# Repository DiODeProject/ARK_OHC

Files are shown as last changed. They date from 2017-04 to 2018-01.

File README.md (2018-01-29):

# ARK - Overhead Controller of Sheffield Robotics

Here we provide the Eagle files (schematics, layouts and gerbers) for the implementation of the new Overhead Controller (OHC) for the Kilobots. 

The bootloader for the microcontroller (Atmega328, 16MHZ) is the same as the Arduino Pro Mini and can be found here: https://github.com/arduino/Arduino/tree/master/hardware/arduino/avr/bootloaders/atmega 

The software for the microcontroller can be found here: https://github.com/acornejo/kilolib. 
Because we use 6 IR LED boards instead of 1, in file `ohc.c` we need to change line 33 to `#define ir_mask 0b00111111 | PORTB`. And then compile on the terminal as `make arduino-ohc-16mhz`.

## Citation
If you make use of or extend this design please cite:

* Nikolaidis, E., Sabo, C., Marshall, J. A. R., Reina, A. (2017) Characterisation and upgrade of the communication between overhead controllers and Kilobots. doi: [10.15131/shef.data.4990910.v2](https://figshare.com/articles/Characterisation_and_upgrade_of_the_communication_between_overhead_controllers_and_Kilobots/4990910)

## See Also
* [KilobotArena](https://github.com/DiODeProject/KilobotArena)
* [Kilobot Wiki](http://diode.group.shef.ac.uk/kilobots/index.php/Kilobots)

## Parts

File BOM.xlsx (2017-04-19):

Board | Name | Quantity | Details | Average cost | Total Cost
Controller | 2.1mm Right Angle PCB Mount DC Power Socket 2.5A | 1 | For the power supply | 0.75 £ | Total cost of the components 12.32 £ Cost of the PCB 50 £ (for 1 board)
 | 2.1mm dc plug | 1 |  | 0.75 £
 | atgmega328-au | 1 | Microcontroller | 4.6 £
 | ft232rl | 1 | Usb to serial interface | 1 £
 | Mount Female Type B USB Connector | 1 |  | 0.45 £
 | BSR802N L6327 N-channel MOSFET | 6 | MOSFET Switches | 1.2 £
 | 22pf Capacitor | 2 | Case 0603 | 0.7 £
 | 0.1uf Capacitor | 7 | Case 0603 | 0.2 £
 | 10uf/50V Capacitor | 1 |  | 0.2 £
 | 470uf/25V Capacitor | 1 |  | 0.6 £
 | 1KΩ Resistor | 2 | Case 0603 | 0.2 £
 | 10KΩ Resistor | 1 |  | 0.1 £
 | 100Ω Resistor | 6 |  | 0.3
 | 47ΚΩ Resistor | 6 |  | 0.07 £
 | 16Mhz Crystal | 1 |  | 0.2 £
 | LED red | 1 | Case 0603 | 0.1 £
 | LED green | 1 |  | 0.1 £
 | SMD tactile push button | 1 |  | 0.3 £
 | female headers 6x1 + 2x1 | 1 |  | 0.3 £
 | male header 3x2 | 1 |  | 0.2 £
IR LED | IR LED TSAL6200 | 10 | Infrared LEDs | 1 £ | Total cost of the components 1.2 £ Cost of the LED PCB 50 £ (for 1 board)
 | 1Ω Resistor | 5 | Case 1206 | 0.2 £

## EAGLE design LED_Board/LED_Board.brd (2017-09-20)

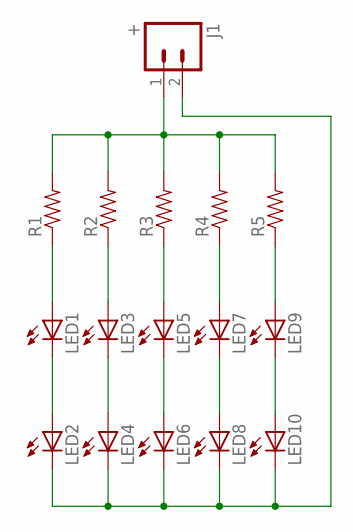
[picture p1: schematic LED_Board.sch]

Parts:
J1: +; 1X02_LOCK
LED1, LED2, LED3, LED4, LED5, LED6, LED7, LED8, LED9, LED10: LED5MM
R1, R2, R3, R4, R5: RESISTOR1206; 1206

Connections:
GND: J1.2, LED2.K (C), LED4.K (C), LED6.K (C), LED8.K (C), LED10.K (C)
unnamed: J1.1, R1.2, R2.2, R3.2, R4.2, R5.2
unnamed: LED9.A, R5.1
unnamed: LED7.A, R4.1
unnamed: LED5.A, R3.1
unnamed: LED3.A, R2.1
unnamed: LED1.A, R1.1
unnamed: LED1.K (C), LED2.A
unnamed: LED3.K (C), LED4.A
unnamed: LED5.K (C), LED6.A
unnamed: LED7.K (C), LED8.A
unnamed: LED9.K (C), LED10.A

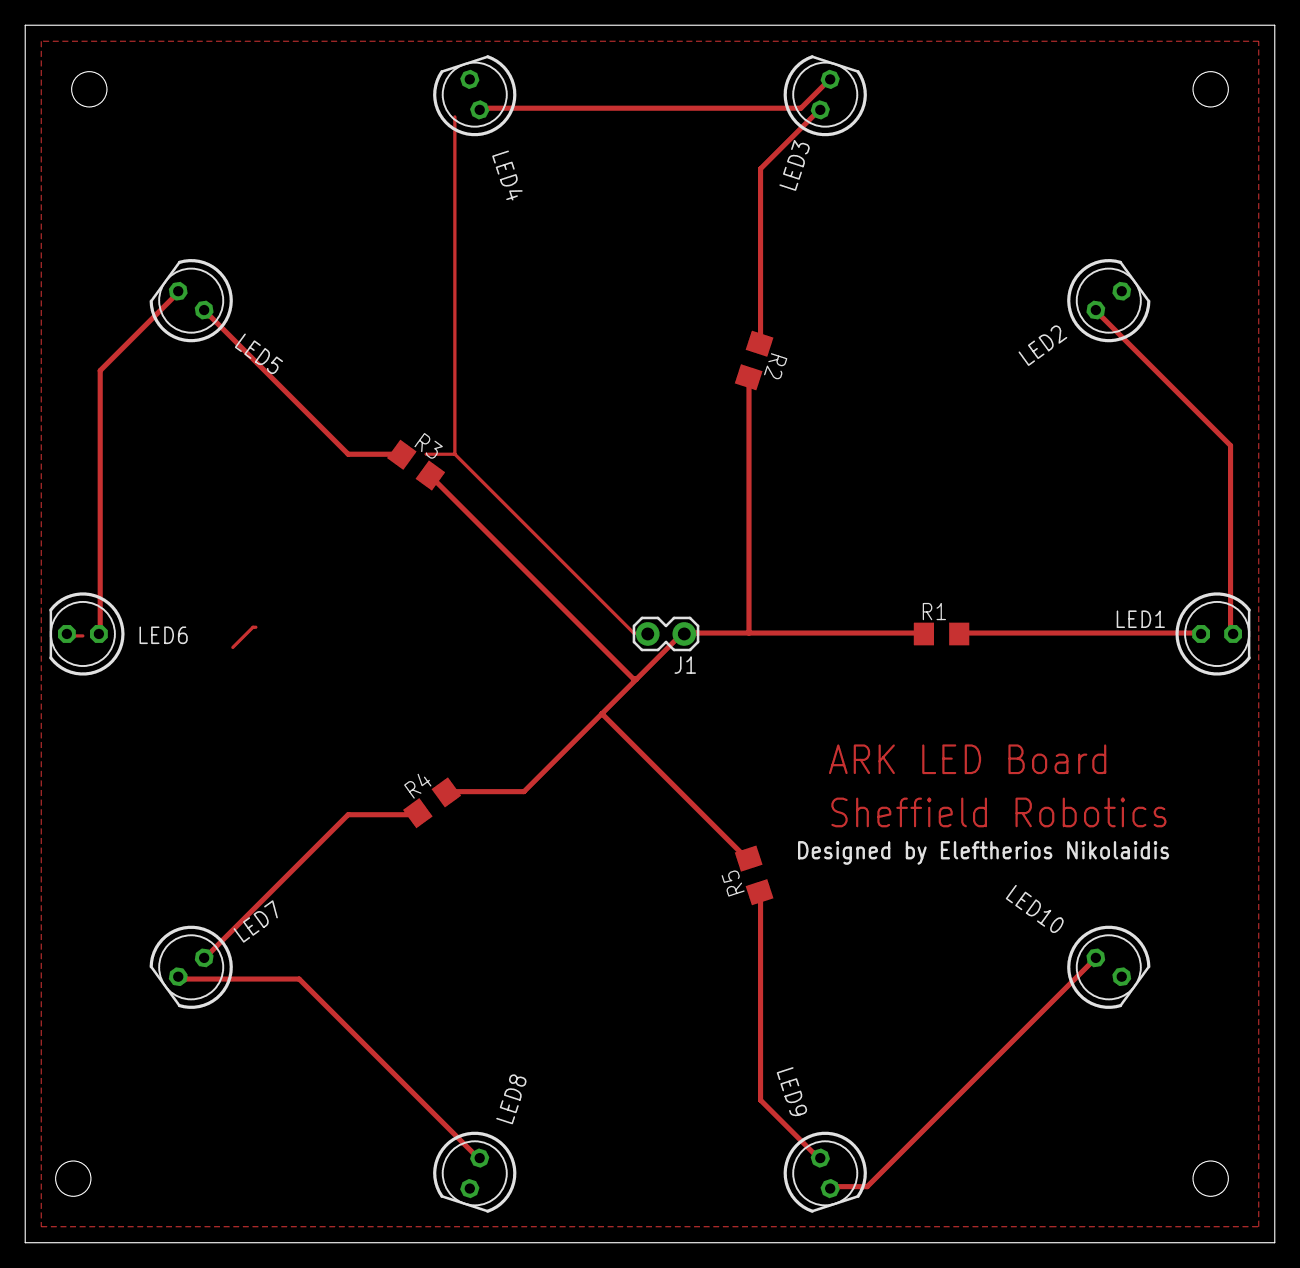
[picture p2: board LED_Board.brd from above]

Board: 2 copper layers, 99.1 x 96.5 mm, 16 parts (0 on the bottom side), 12 nets.

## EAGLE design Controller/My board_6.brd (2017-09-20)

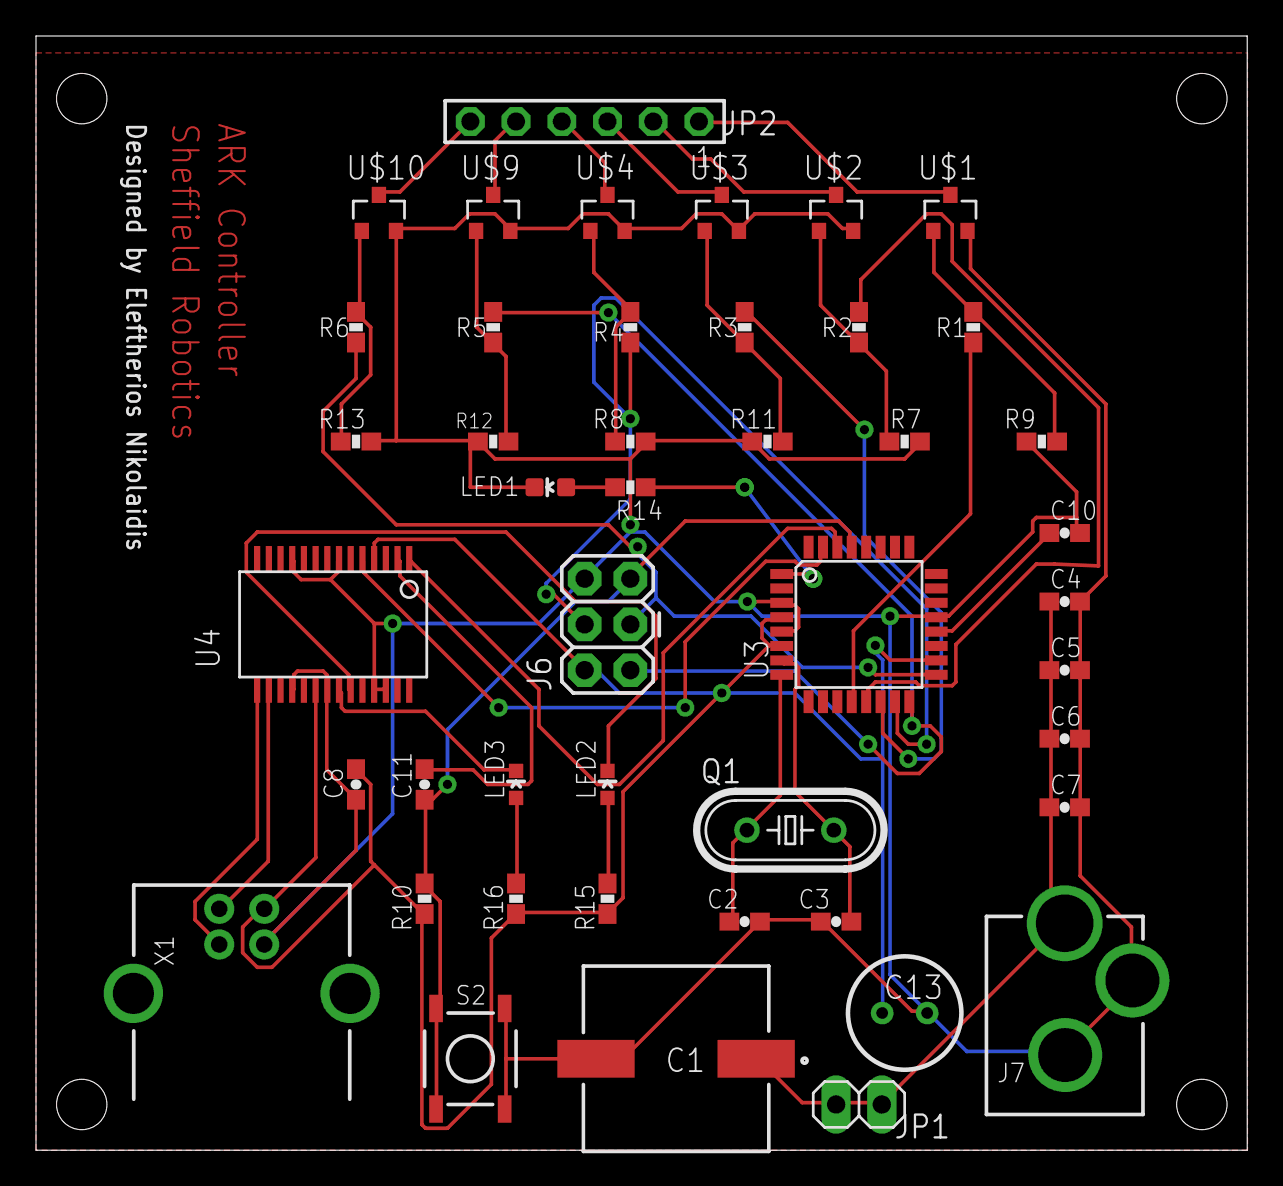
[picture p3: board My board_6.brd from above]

Board: 2 copper layers, 67.3 x 61.9 mm, 45 parts (0 on the bottom side), 36 nets.

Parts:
C1: EEEFK1E471P; ALUMINUM-ELECTROLYTIC-CAPACITO
C2, C3: 22pf; 0603-CAP
C4, C5, C6, C7, C8, C10, C11: 0.1uF; 0603-CAP
C13: 10uF; ECEA1HKS100B
J6: ICSP; 2X3
J7: POWER_JACK; POWER_JACK_PTH_LOCK
JP1: 1X02
JP2: TSW-106-02-S-S
LED1, LED3: Green; LED-0603
LED2: Red; LED-0603
Q1: HC49/S
R1, R2, R3, R4, R5, R6: 100; 0603-RES
R7, R8, R9, R11, R12, R13: 47k; 0603-RES
R10: 10K; 0603-RES
R14, R15, R16: 1K; 0603-RES
S2: Reset; TACTILE-SWITCH-SMD-ALT01
U3: ATMEGA328; TQFP32-08
U4: FT232RL; SSOP28DB
U$1, U$2, U$3, U$4, U$9: SOT23-3
U$10: N-CHANNEL-MOSFETs-BSS138; SOT23-3
X1: USB-B; USB-B-PTH

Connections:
AREF: C10.2, U3.20
DTR1: C11.2, U4.2
GND: C1.2, C2.2, C3.2, C4.2, C5.2, C6.2, C7.2, C8.2, C10.1, C13.2, J6.6, J7.GND, J7.GNDBREAK, LED1.C, R7.2, R8.2, R9.2, R11.2, R12.2, R13.2, S2.1, S2.2, U3.3, U3.5, U3.21, U4.7, U4.11, U4.18, U4.21, U4.25, U4.26, U$1.2, U$2.2, U$3.2, U$4.2, U$9.2, U$10.2, X1.GND
unnamed: JP2.5, U$9.3
unnamed: JP2.6, U$10.3
unnamed: R3.2, U3.14
unnamed: R2.1, R7.1, U$2.1
unnamed: R3.1, R11.1, U$3.1
unnamed: R1.1, R9.1, U$1.1
unnamed: R4.1, R8.1, U$4.1
unnamed: R5.1, R12.1, U$9.1
unnamed: R6.1, R13.1, U$10.1
unnamed: C2.1, Q1.1, U3.8
unnamed: C3.1, Q1.2, U3.7
unnamed: LED2.A, R15.1
unnamed: LED3.A, R16.1
unnamed: U3.30, U4.1
unnamed: R1.2, U3.12
unnamed: R2.2, U3.13
unnamed: J6.4, R4.2, U3.15
unnamed: JP2.1, U$1.3
unnamed: JP2.2, U$2.3
unnamed: JP2.3, U$3.3
unnamed: JP2.4, U$4.3
unnamed: J6.1, R5.2, U3.16
unnamed: C1.1, C4.1, C5.1, C6.1, C7.1, J7.PWR, JP1.1, JP1.2
RESET: C11.1, J6.5, R10.1, S2.3, S2.4, U3.29
RXLED1: LED3.C, U4.22
S$1: U3.31, U4.5
S$4: R14.2, U3.1
S$5: LED1.A, R14.1
SCK1: J6.3, R6.2, U3.17
TXLED1: LED2.C, U4.23
USB_D+1: U4.15, X1.D+
USB_D-1: U4.16, X1.D-
VCCIO: C8.1, C13.1, J6.2, R10.2, R15.2, R16.2, U3.4, U3.6, U3.18, U4.4, U4.20, X1.VBUS

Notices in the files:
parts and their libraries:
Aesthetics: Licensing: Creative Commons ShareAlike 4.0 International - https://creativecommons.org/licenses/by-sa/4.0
